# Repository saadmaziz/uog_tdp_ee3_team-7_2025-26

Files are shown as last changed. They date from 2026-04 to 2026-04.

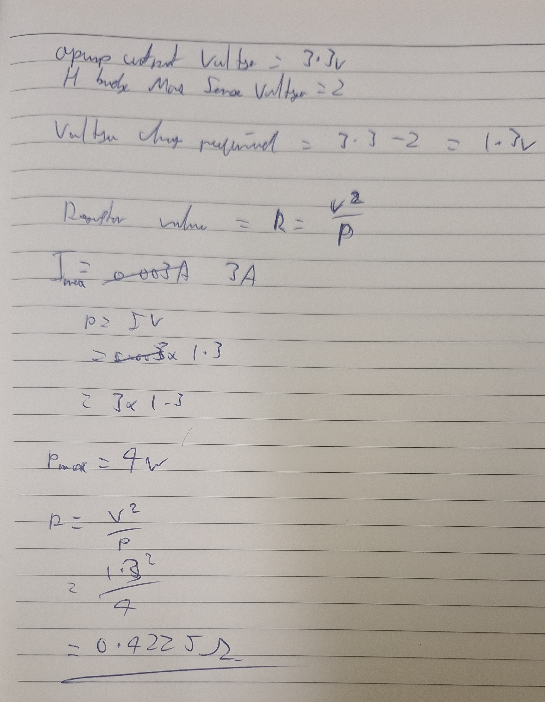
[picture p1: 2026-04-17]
5 - Research, Datasheets, and Manuals/5-1 - Research/calculations/H-bridge resistor calculation.jpg

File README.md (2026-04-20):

# UoG_TDP-EE3_Team_7
Design Files for the 3rd year EEE team design project at the University of Glasgow. Line following rover, with obstacle avoidance, traffic lights detection, remote control using an ESP-32 connected to a laptop and a Logitech 3D Pro Joystick.
The  Centeral processor is a Freescale NXP Frdm KL25Z.

1 - Team Organisation and 6 - General Documents are not uploaded as they may contain non-relavant information that should not be made public

The team consisted of 5 members.

My personal contributions spanned all of the software, all of the mechanical design, a substantial part of the electronic hardware design, and most of the integration.

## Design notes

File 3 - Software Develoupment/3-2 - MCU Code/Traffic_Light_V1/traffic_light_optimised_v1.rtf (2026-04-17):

#include "mbed.h"

#include <algorithm> // std::max

#include <cmath> // roundf

// 7-bit I2C address is 0x10; mbed I2C wants 8-bit address (shifted left)
#define VEML3328_ADDR (0x10 << 1) // 0x20

#define REG_CONFIG 0x00

#define REG_R_DATA 0x05

#define REG_G_DATA 0x06

#define REG_B_DATA 0x07

I2C i2c(PTC2, PTC1);

PwmOut led_R(LED_RED);
PwmOut led_G(LED_GREEN);
PwmOut led_B(LED_BLUE);

// Tuning knobs
static const float PWM_PERIOD_S = 0.001f; // 1 kHz PWM
static const float EMA_ALPHA = 0.25f; // 0..1 (higher = more responsive, lower = smoother)
static const float MIN_SCALE = 50.0f; // prevents divide-by-zero
static const int ROUND_STEPS = 30; // your roundingfactor

static inline float clamp01(float x) {
if (x < 0.0f) return 0.0f;
if (x > 1.0f) return 1.0f;
return x;
}

uint16_t read_reg(uint8_t reg) {
char cmd[1] = { (char)reg };
char data[2] = { 0, 0 };

int w = i2c.write(VEML3328_ADDR, cmd, 1, true);
int r = i2c.read(VEML3328_ADDR, data, 2, false);

if (w != 0 || r != 0) {
return 0; // basic fail-safe
}

return (uint16_t)((uint8_t)data[1] << 8) | (uint8_t)data[0];
}

int main() {
// I2C speed
i2c.frequency(400000); // 400 kHz

// Sensor config: 0x0000 (powers on, default gain/IT per datasheet defaults)
char config_cmd[3] = { REG_CONFIG, 0x00, 0x00 };
i2c.write(VEML3328_ADDR, config_cmd, 3, false);

// PWM setup (ALL channels)
led_R.period(PWM_PERIOD_S);
led_G.period(PWM_PERIOD_S);
led_B.period(PWM_PERIOD_S);

// EMA filtered values
float r_f = 0.0f, g_f = 0.0f, b_f = 0.0f;

while (true) {
uint16_t r_raw = read_reg(REG_R_DATA);
uint16_t g_raw = read_reg(REG_G_DATA);
uint16_t b_raw = read_reg(REG_B_DATA);

// Smooth raw readings
r_f = (1.0f - EMA_ALPHA) * r_f + EMA_ALPHA * (float)r_raw;
g_f = (1.0f - EMA_ALPHA) * g_f + EMA_ALPHA * (float)g_raw;
b_f = (1.0f - EMA_ALPHA) * b_f + EMA_ALPHA * (float)b_raw;

// Auto-scale
float max_rgb = std::max({r_f, g_f, b_f});
if (max_rgb < MIN_SCALE) max_rgb = MIN_SCALE;

float r_norm = r_f / max_rgb;
float g_norm = g_f / max_rgb;
float b_norm = b_f / max_rgb;

// Rounding
r_norm = roundf(r_norm * ROUND_STEPS) / ROUND_STEPS;
g_norm = roundf(g_norm * ROUND_STEPS) / ROUND_STEPS;
b_norm = roundf(b_norm * ROUND_STEPS) / ROUND_STEPS;

r_norm = clamp01(r_norm);
g_norm = clamp01(g_norm);
b_norm = clamp01(b_norm);

// KL25Z LEDs are active low
led_R = 1.0f - r_norm;
led_G = 1.0f - g_norm;
led_B = 1.0f - b_norm;

ThisThread::sleep_for(50ms); // quicker refresh
}
}

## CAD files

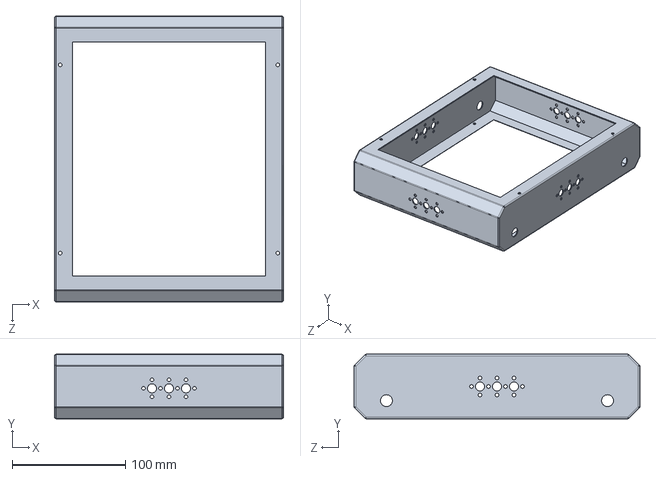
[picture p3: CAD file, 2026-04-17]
4 - Mechanical CAD/Chassis/Main Chassis.SLDPRT
202.0 x 57.0 x 252.0 mm

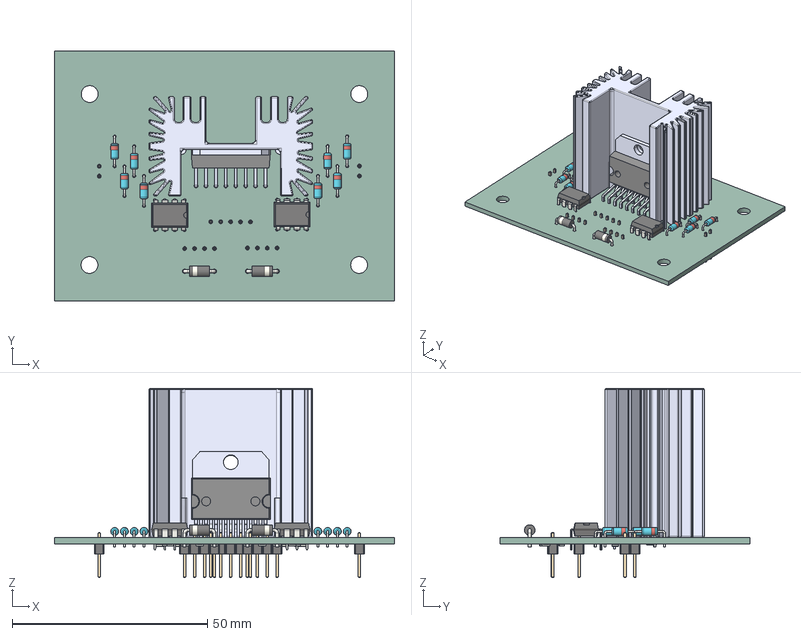
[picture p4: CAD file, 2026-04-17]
2 - PCB Files/2-1 - Distribution Board/Distribution Board V2/$tempfile$.step
87.0 x 64.0 x 48.4 mm
D_DO-35_SOD27_P7.62mm_Horizontal x 8
D_DO-41_SOD81_P7.62mm_Horizontal x 2
DIP-8_W7.62mm x 2
L298N
36-0275_Heatsink
PinHeader_1x04_P2.54mm_Vertical x 2
PinHeader_1x02_P2.54mm_Vertical x 2
R_0805_2012Metric x 10
PinHeader_1x05_P2.54mm_Vertical
C_0805_2012Metric x 2
R_1206_3216Metric x 4
TDP3_T7_H-Bridge_V-3_PCB

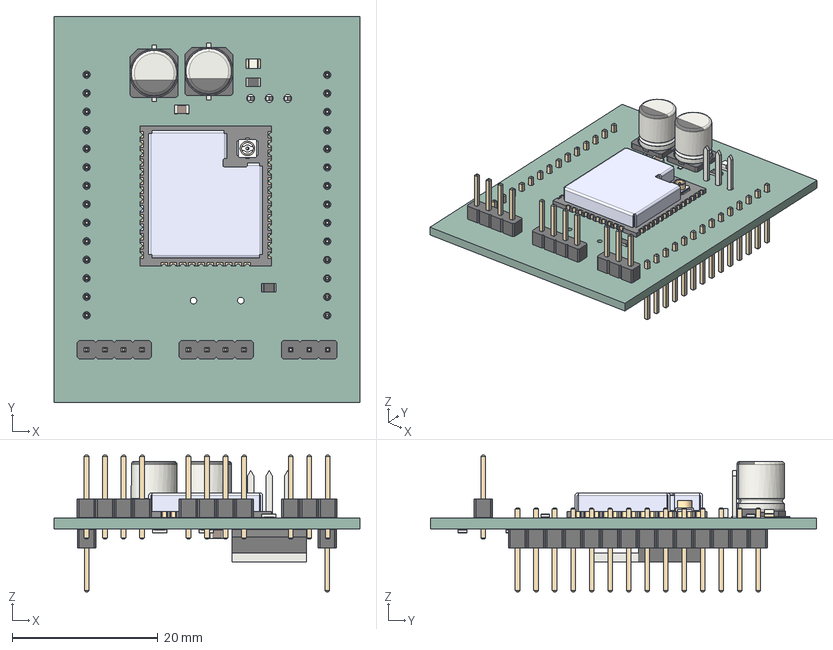
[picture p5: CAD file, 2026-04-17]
2 - PCB Files/2-1 - Distribution Board/Distribution Board V2/PCBs/ESP32-Breakout V1.step
42.0 x 53.0 x 18.8 mm
LED_0805_2012Metric
CP_Elec_6.3x7.7 x 2
PinHeader_1x04_P2.54mm_Vertical x 2
R_0805_2012Metric x 4
ESP32-WROOM-32UE-N4
C_0805_2012Metric x 3
PinHeader_1x03_P2.54mm_Vertical
PinHeader_1x14_P2.54mm_Vertical x 2
TO-220-3_Horizontal_TabUp
ESP32_Breakout V1_PCB

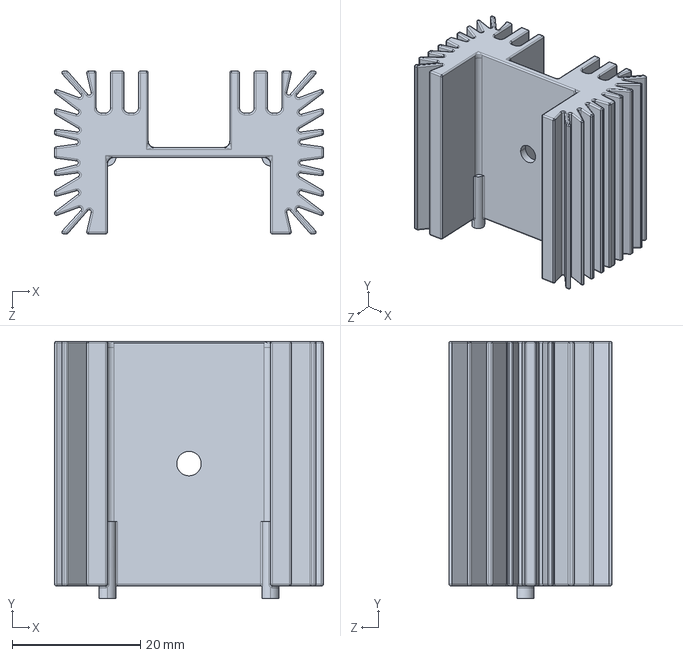
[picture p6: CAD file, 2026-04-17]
2 - PCB Files/2-2 - Motor Driver/heatsink.STEP
41.9 x 40.1 x 25.4 mm

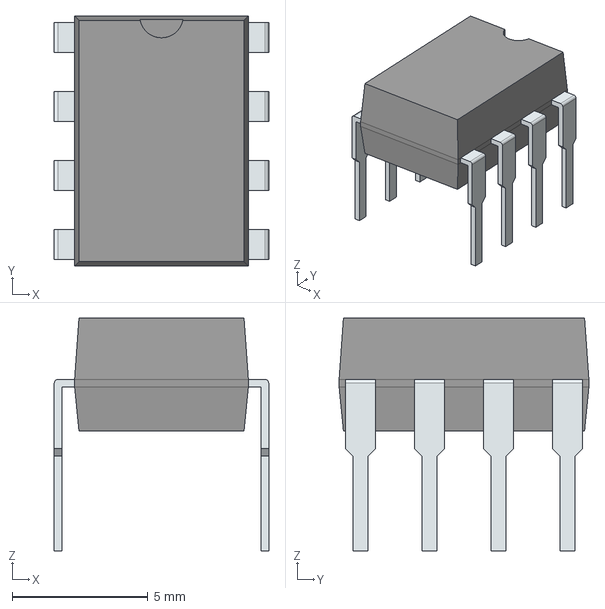
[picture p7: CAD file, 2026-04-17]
2 - PCB Files/2-2 - Motor Driver/TDP3_T7_H-Bridge_V-3/TDP3_T7_H-Bridge_V-3/LF353N.stp
7.90 x 9.20 x 8.58 mm
PinsArrayLR

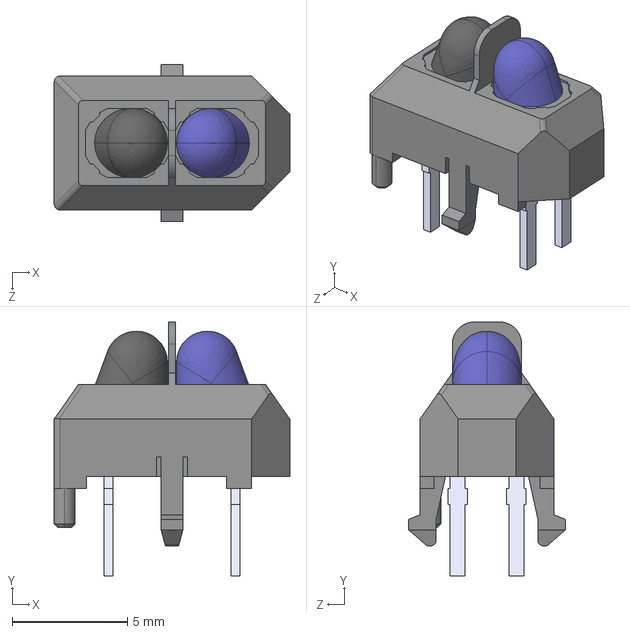
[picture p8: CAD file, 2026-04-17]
2 - PCB Files/2-3 - Line Following/Line following V3/TCRT5000.stp
10.2 x 11.0 x 6.80 mm

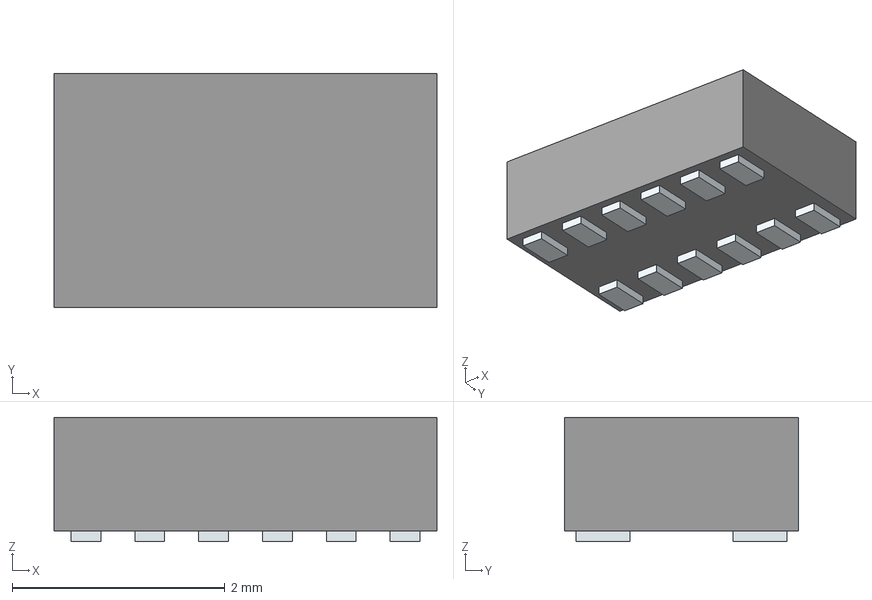
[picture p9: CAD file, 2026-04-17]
2 - PCB Files/2-5 - Obstacle Avoidance/Breakout OSRAM_TMF8806-1AM V1/TMF8806/TMF8806-1AM_OLGA12_LF_T&RDP.stp
3.60 x 2.20 x 1.17 mm
Pins

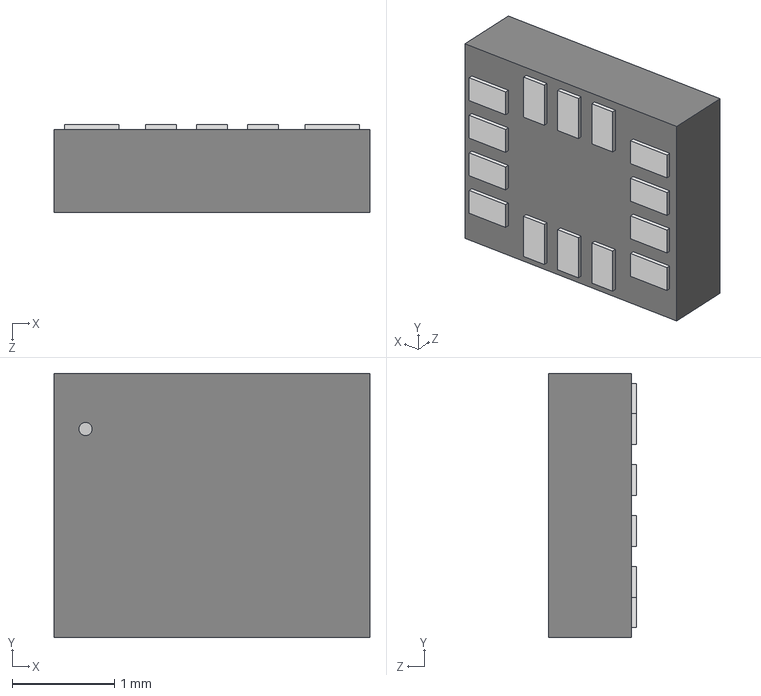
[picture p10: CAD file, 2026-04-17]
2 - PCB Files/2-5 - Obstacle Avoidance/Breakout STM-LSM6DSOQTR V1/LSM6DSO.stp
3.10 x 2.59 x 0.866 mm

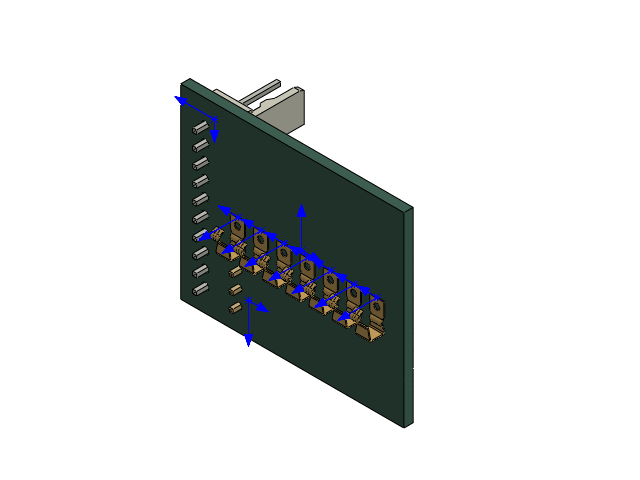
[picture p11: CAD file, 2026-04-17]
4 - Mechanical CAD/PCBs/LiDAR/Slip Ring Static Contacts PCB V2 SLD1.SLDASM
S7171-45R.step x 7
Molex_KK-254_AE-6410-10A_1x10_P2.54mm_Vertical.step
PinHeader_1x03_P2.54mm_Vertical.step
Slip Ring Stactic Contacts V2_PCB.step

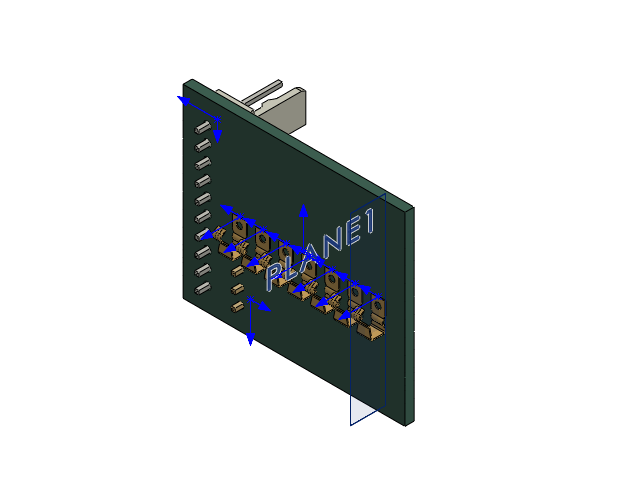
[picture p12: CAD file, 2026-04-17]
4 - Mechanical CAD/LiDAR(Sonar)/V2/PCBs/Slip Ring Static Contacts PCB V2 SLD1/Slip Ring Static Contacts PCB V2 SLD1.SLDASM
S7171-45R.step x 7
Molex_KK-254_AE-6410-10A_1x10_P2.54mm_Vertical.step
PinHeader_1x03_P2.54mm_Vertical.step
Slip Ring Stactic Contacts V2_PCB.step

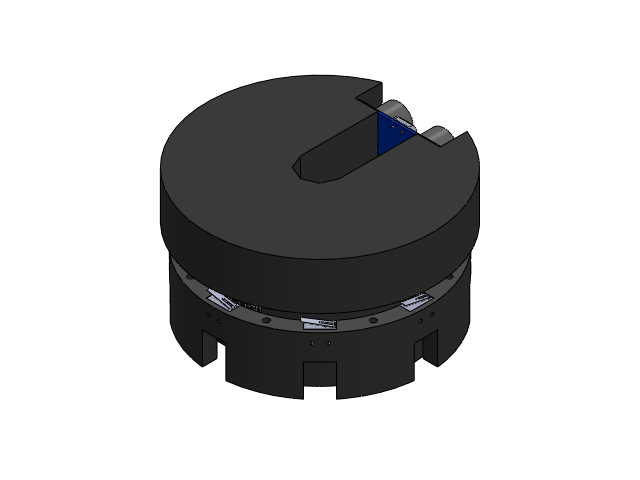
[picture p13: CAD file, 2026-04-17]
4 - Mechanical CAD/LiDAR(Sonar)/V2/Sonar Assembly.SLDASM
Base
FS09R_Servo_Motor
AC6000Z-ISB_Bearing
S7171-45R.step x 7
Molex_KK-254_AE-6410-10A_1x10_P2.54mm_Vertical.step
PinHeader_1x03_P2.54mm_Vertical.step
Slip Ring Stactic Contacts V2_PCB.step
Slip Ring Rotating Contacts V2_PCB.step
Center
Spinny_Top
Switch holder
Encoding Switch x 8
Switch Peg
Ultrasonic sensor

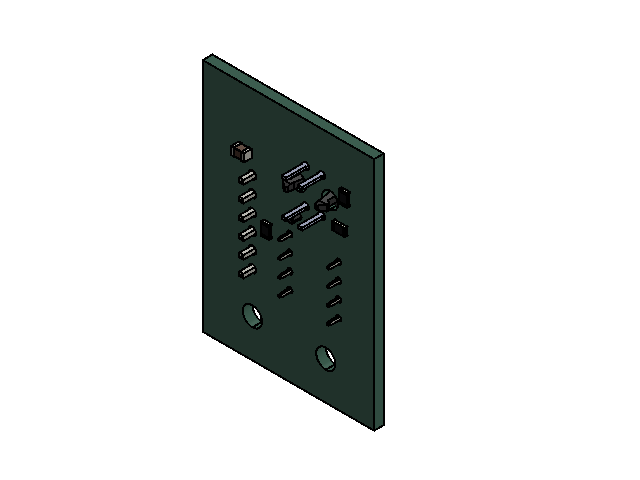
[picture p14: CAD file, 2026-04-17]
4 - Mechanical CAD/Line Sensors/Line Following Side.SLDASM
C_0805_2012Metric_1.step
R_0805_2012Metric_1.step x 3
Molex_KK-254_AE-6410-06A_1x06_P2.54mm_Vertical.step
TCRT5000_1.step
DIP-8_W7.62mm_1.step
Line following V3_PCB.step

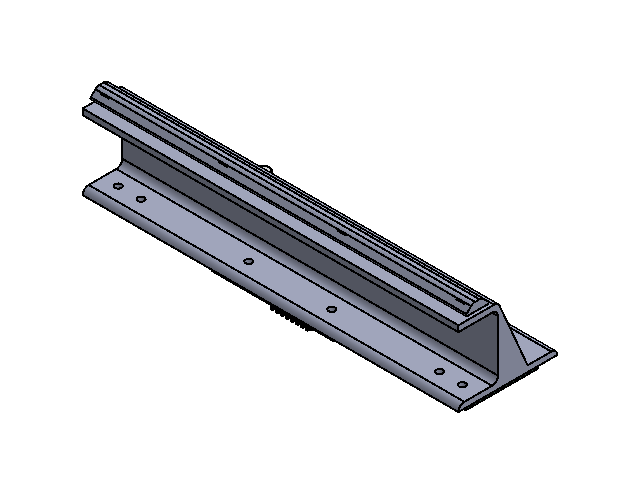
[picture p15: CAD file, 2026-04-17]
4 - Mechanical CAD/Line Sensors/Line Following Assem.SLDASM
Mount
R_0805_2012Metric.step x 12
C_0805_2012Metric.step x 2
TCRT5000.step x 3
DIP-8_W7.62mm.step x 3
Molex_KK-254_AE-6410-08A_1x08_P2.54mm_Vertical.step
Line following V2_PCB.step
Molex_KK-254_AE-6410-06A_1x06_P2.54mm_Vertical_1.step
TCRT5000_2.step
DIP-8_W7.62mm_2.step
C_0805_2012Metric_2.step
R_0805_2012Metric_2.step x 3
Line following V3_PCB_1.step
Pot
C_0805_2012Metric_1.step
R_0805_2012Metric_1.step x 3
Molex_KK-254_AE-6410-06A_1x06_P2.54mm_Vertical.step
TCRT5000_1.step
DIP-8_W7.62mm_1.step
Line following V3_PCB.step
Nut_Holder

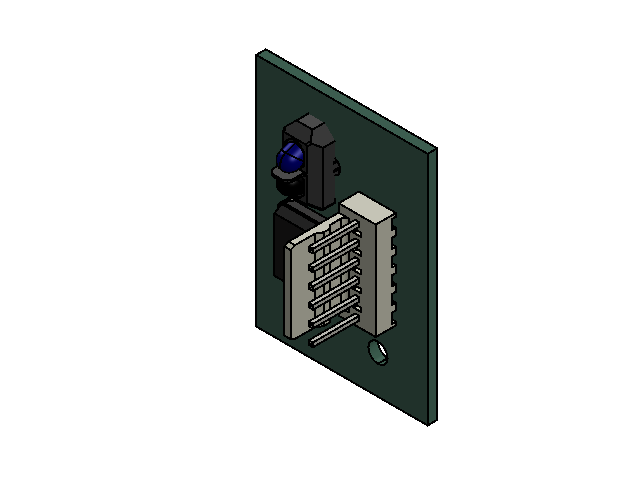
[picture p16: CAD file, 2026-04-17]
4 - Mechanical CAD/Line Sensors/Line Following Side mirrored.SLDASM
Molex_KK-254_AE-6410-06A_1x06_P2.54mm_Vertical_1.step
TCRT5000_2.step
DIP-8_W7.62mm_2.step
C_0805_2012Metric_2.step
R_0805_2012Metric_2.step x 3
Line following V3_PCB_1.step

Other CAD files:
4 - Mechanical CAD/LiDAR(Sonar)/V2/PCBs/Slip Ring Rotating Contacts PCB V2 SLD/Slip Ring Rotating Contacts PCB V2 SLD.SLDASM
4 - Mechanical CAD/Scissor Jack/Assem.SLDASM
4 - Mechanical CAD/PCBs/LiDAR/Slip Ring Rotating Contacts PCB V2 SLD.SLDASM
4 - Mechanical CAD/Line Sensors/Line Following Center.SLDASM
2 - PCB Files/2-1 - Distribution Board/Distribution Board V2/PCBs/Motor-Controller.step
2 - PCB Files/2-1 - Distribution Board/Distribution Board V2/PCBs/Power-Supply.step
2 - PCB Files/2-2 - Motor Driver/36-0275_Heatsink.STEP
2 - PCB Files/2-2 - Motor Driver/L298N.stp
2 - PCB Files/2-5 - Obstacle Avoidance/LiDAR Distance Measurement V1/TMF8806/Breakout OSRAM_TMF8806-1AM V1.step
2 - PCB Files/2-5 - Obstacle Avoidance/LiDar Baseboard (Angle Measurement) V1/Breakout STM-LSM6DSOQTR V1.step
2 - PCB Files/2-5 - Obstacle Avoidance/LiDar Baseboard (Angle Measurement) V1/LSM6DSOTR.stp
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

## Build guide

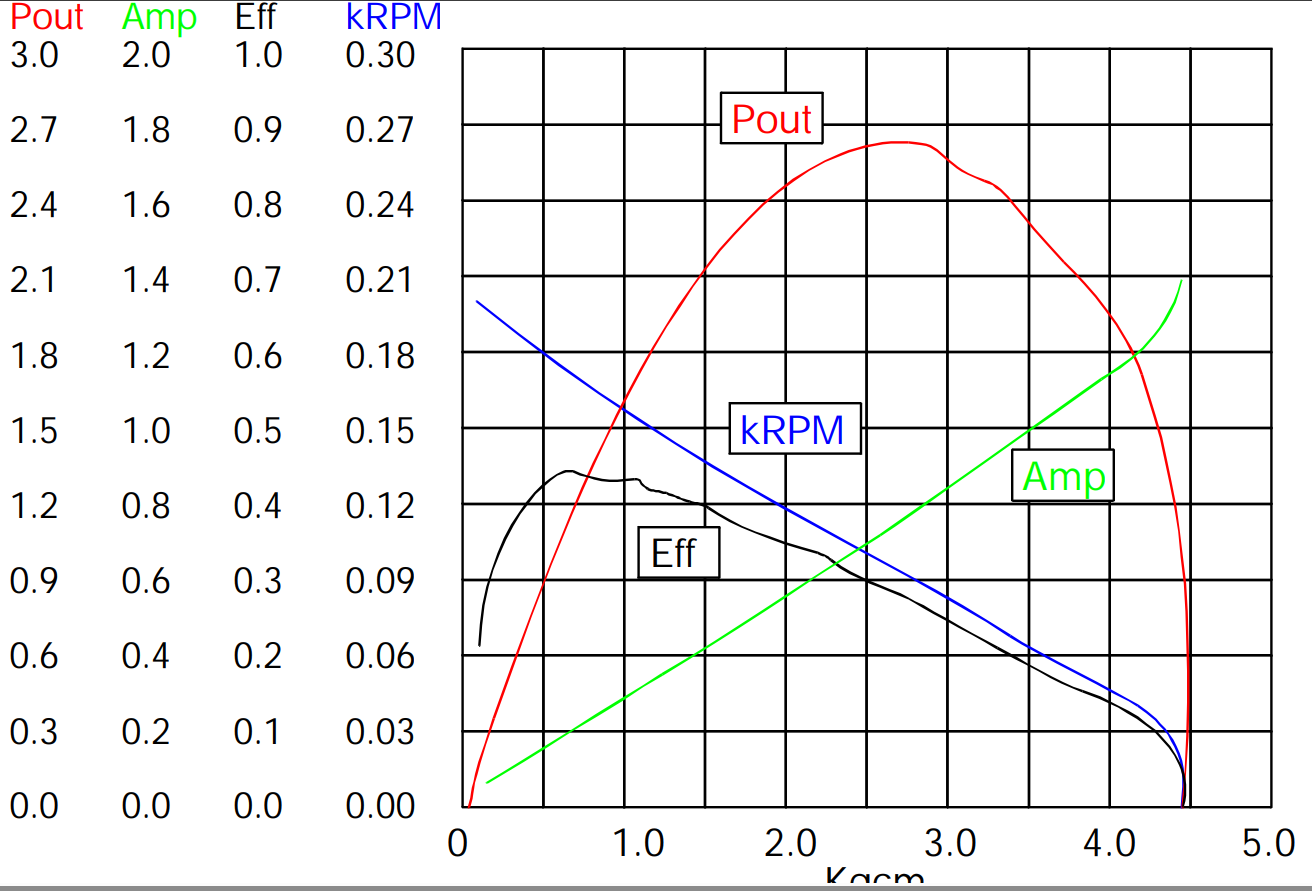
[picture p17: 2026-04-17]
5 - Research, Datasheets, and Manuals/5-1 - Research/Motor Curves/Motor Plot.PNG

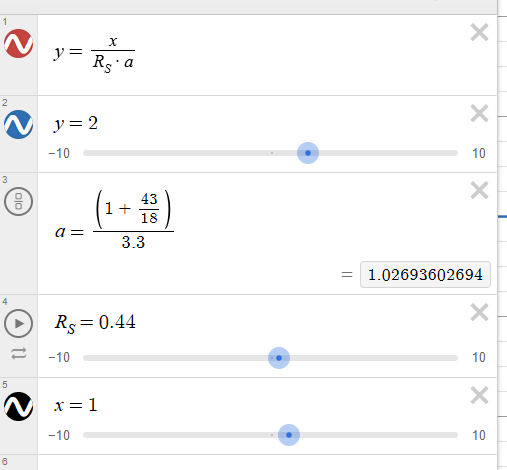
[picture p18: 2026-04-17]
5 - Research, Datasheets, and Manuals/5-1 - Research/Motor Curves/I-RPM transfrer.PNG

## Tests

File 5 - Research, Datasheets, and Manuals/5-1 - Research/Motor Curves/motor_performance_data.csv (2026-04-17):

Torque (Kgcm) | Pout (Output Power) | Amp (Current) | Eff (Efficiency) | kRPM (Speed)
0 | 0 | 0 | 0 | 200
0.5 | 0.85 | 0.32 | 0.44 | 178
1 | 1.55 | 0.53 | 0.42 | 155
1.5 | 2.1 | 0.74 | 0.38 | 133
2 | 2.45 | 0.95 | 0.34 | 111
2.5 | 2.65 | 1.16 | 0.3 | 89
3 | 2.55 | 1.37 | 0.24 | 67
3.5 | 2.2 | 1.58 | 0.18 | 44
4 | 1.6 | 1.79 | 0.12 | 22
4.5 | 0 | 2 | 0 | 0
 | 2.65
 | y = -97.659x + 200

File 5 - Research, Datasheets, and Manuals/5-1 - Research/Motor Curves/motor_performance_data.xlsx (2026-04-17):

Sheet: motor_performance_data
Torque (Kgcm) | Pout (Output Power) | Amp (Current) | Eff (Efficiency) | RPM (Speed)
0 | 0 | 0 | 0 | 200
0.5 | 0.85 | 0.32 | 0.44 | 178
1 | 1.55 | 0.53 | 0.42 | 155
1.5 | 2.1 | 0.74 | 0.38 | 133
2 | 2.45 | 0.95 | 0.34 | 111
2.5 | 2.65 | 1.16 | 0.3 | 89
3 | 2.55 | 1.37 | 0.24 | 67
3.5 | 2.2 | 1.58 | 0.18 | 44
4 | 1.6 | 1.79 | 0.12 | 22
4.5 | 0 | 2 | 0 | 0
 | 2.65
 | I to RPM | RPM to M/S
 | y = -97.659x + 200 | M/s = RPM* 0.012566
 | 1.9
 | 14.4479

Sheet: Sheet1
Amp (Current) | Torque (Kgcm)
0 | 0
0.32 | 0.5
0.53 | 1
0.74 | 1.5
0.95 | 2
1.16 | 2.5
1.37 | 3
1.58 | 3.5
1.79 | 4
2 | 4.5

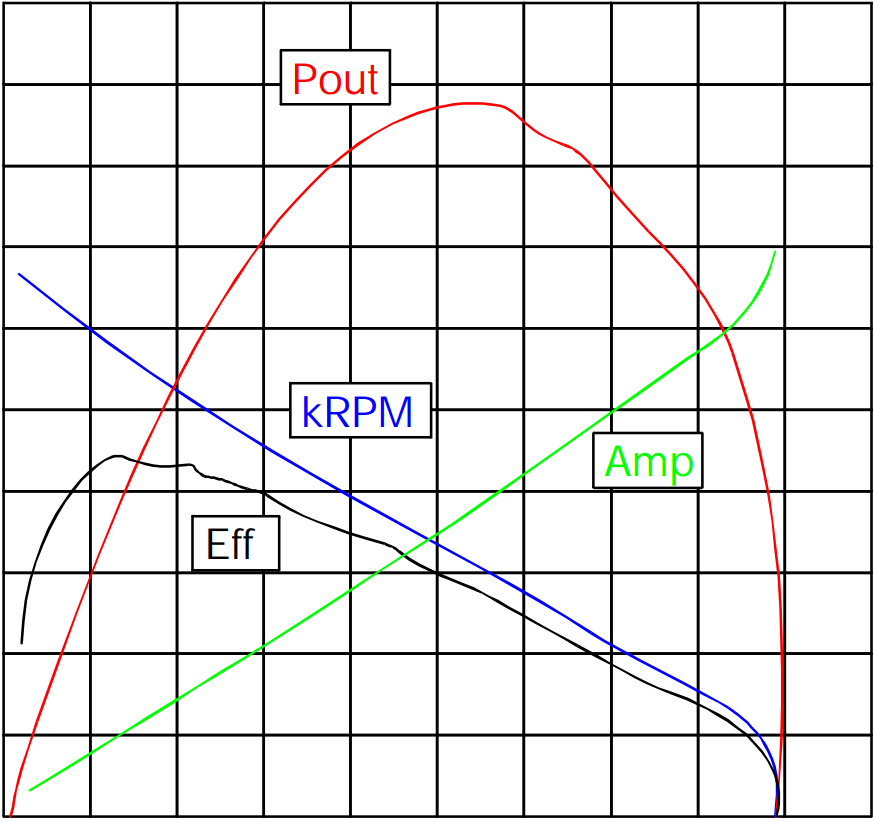
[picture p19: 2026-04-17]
5 - Research, Datasheets, and Manuals/5-1 - Research/Position measurement/Motor Plot.PNG

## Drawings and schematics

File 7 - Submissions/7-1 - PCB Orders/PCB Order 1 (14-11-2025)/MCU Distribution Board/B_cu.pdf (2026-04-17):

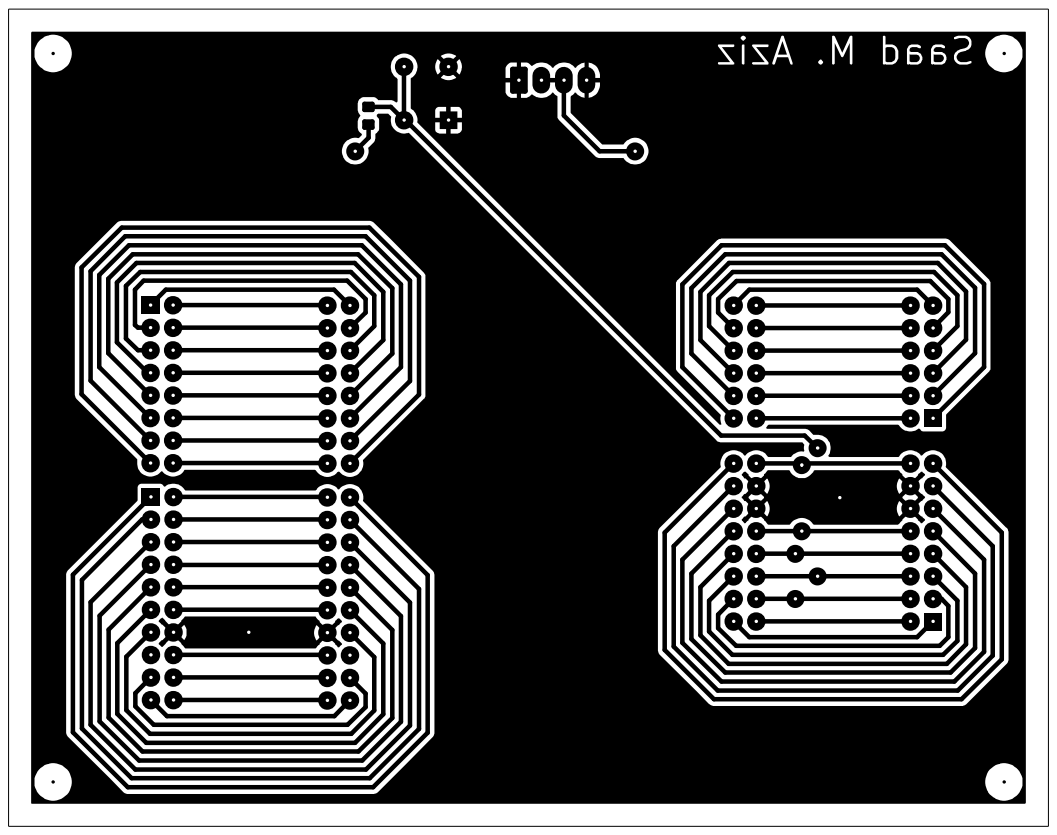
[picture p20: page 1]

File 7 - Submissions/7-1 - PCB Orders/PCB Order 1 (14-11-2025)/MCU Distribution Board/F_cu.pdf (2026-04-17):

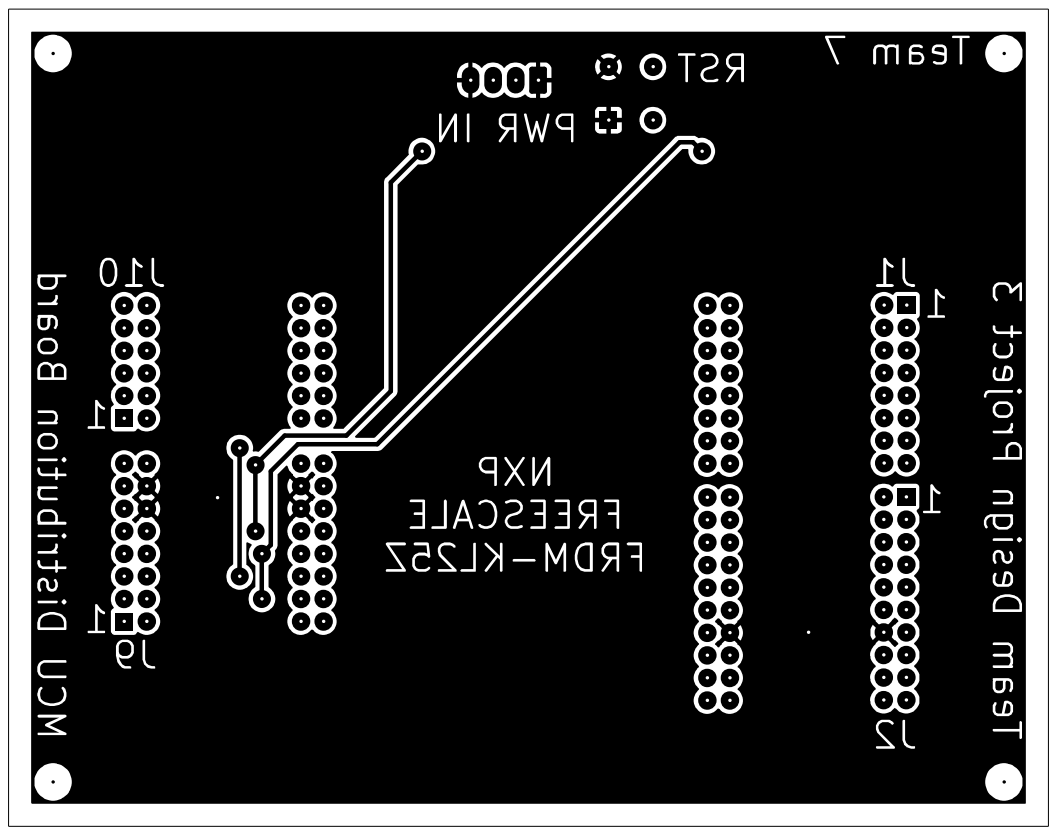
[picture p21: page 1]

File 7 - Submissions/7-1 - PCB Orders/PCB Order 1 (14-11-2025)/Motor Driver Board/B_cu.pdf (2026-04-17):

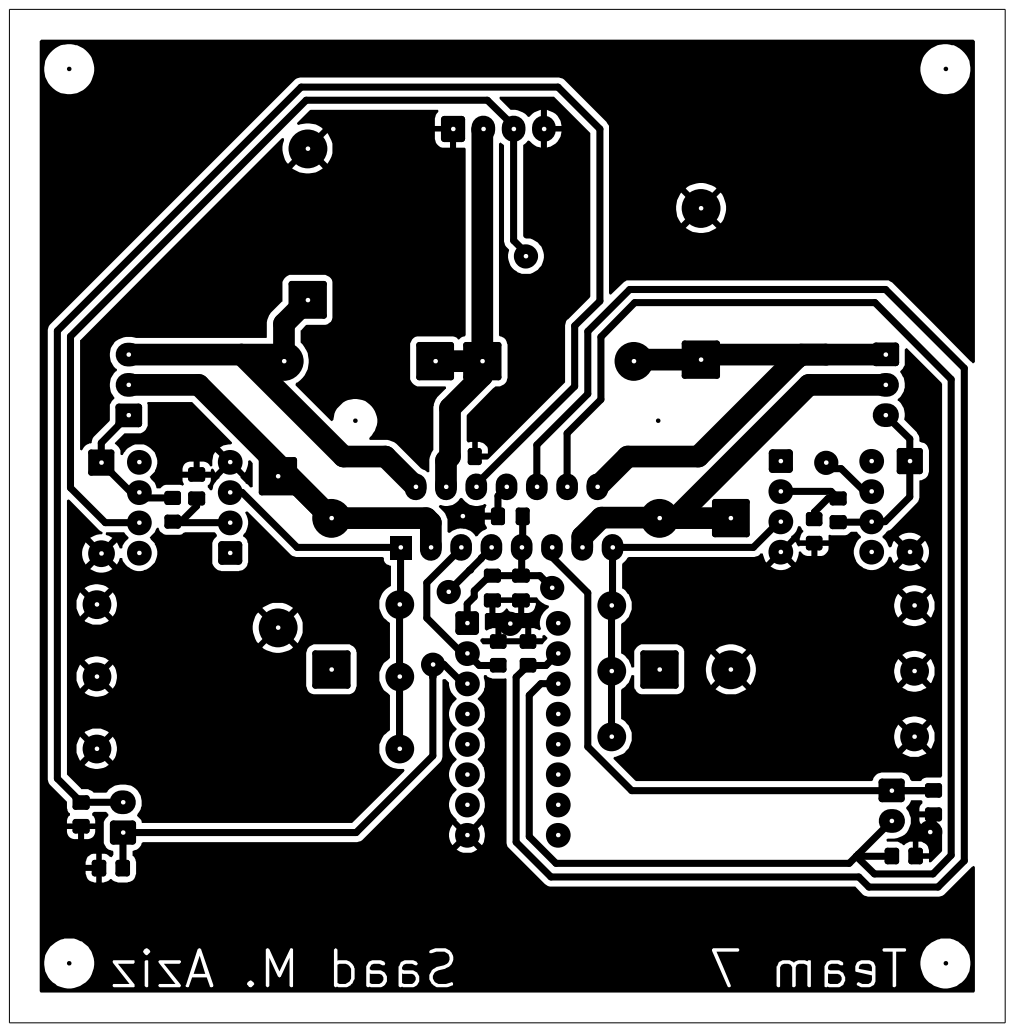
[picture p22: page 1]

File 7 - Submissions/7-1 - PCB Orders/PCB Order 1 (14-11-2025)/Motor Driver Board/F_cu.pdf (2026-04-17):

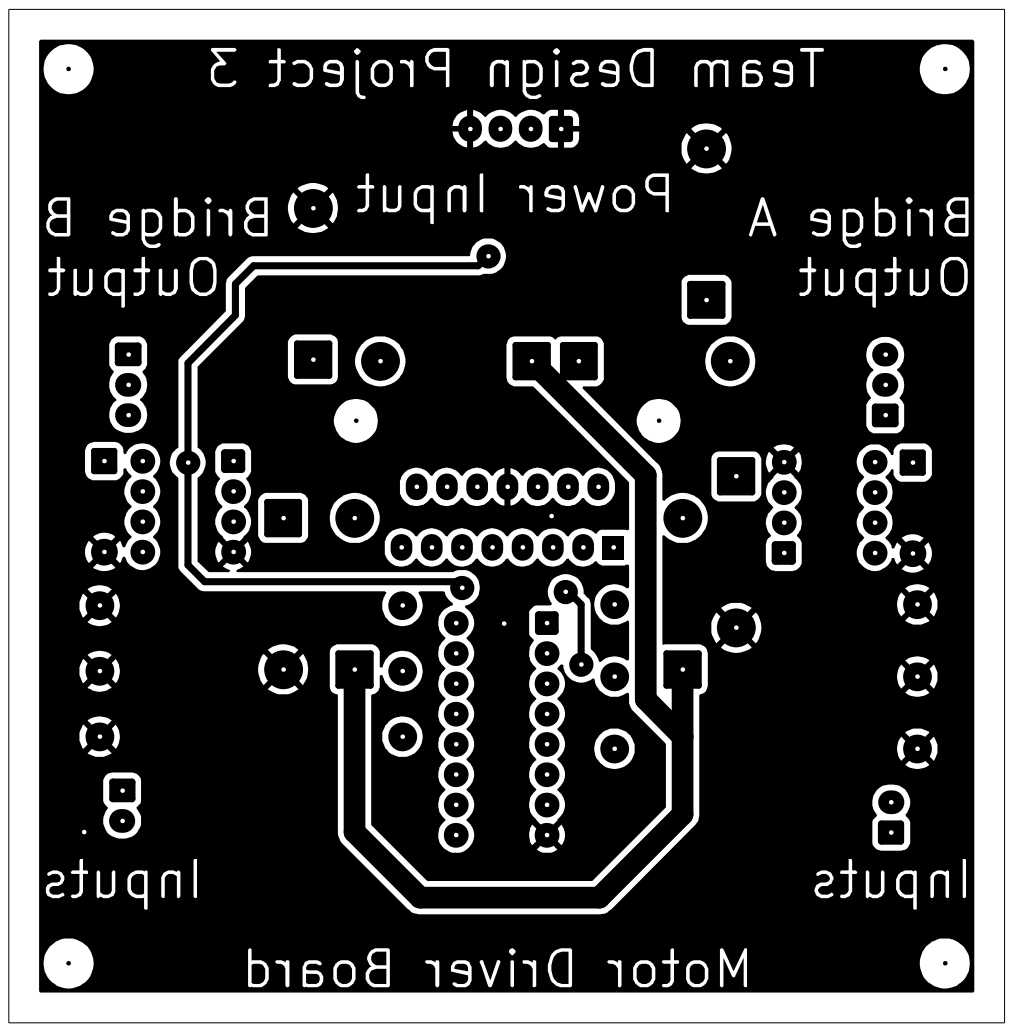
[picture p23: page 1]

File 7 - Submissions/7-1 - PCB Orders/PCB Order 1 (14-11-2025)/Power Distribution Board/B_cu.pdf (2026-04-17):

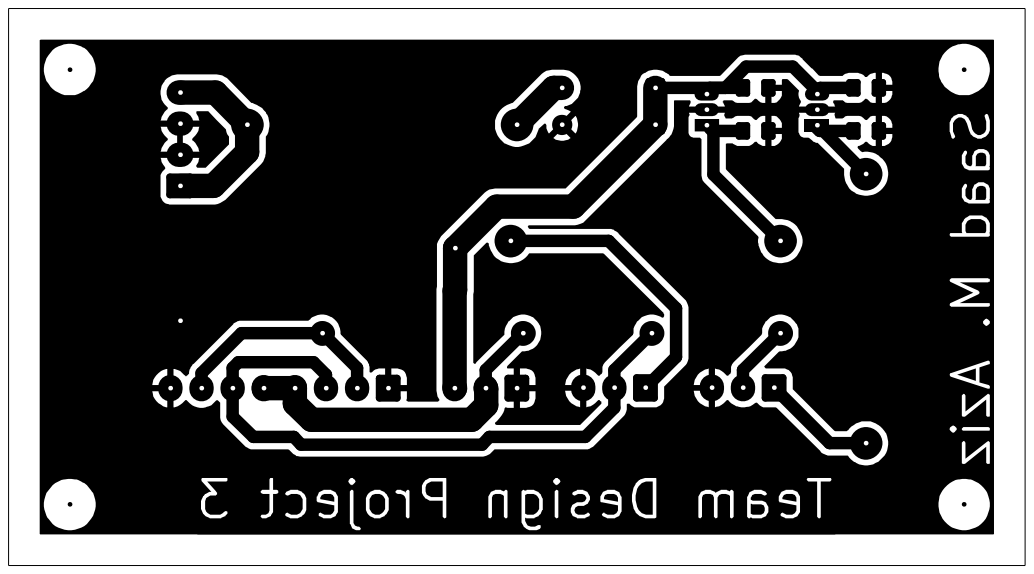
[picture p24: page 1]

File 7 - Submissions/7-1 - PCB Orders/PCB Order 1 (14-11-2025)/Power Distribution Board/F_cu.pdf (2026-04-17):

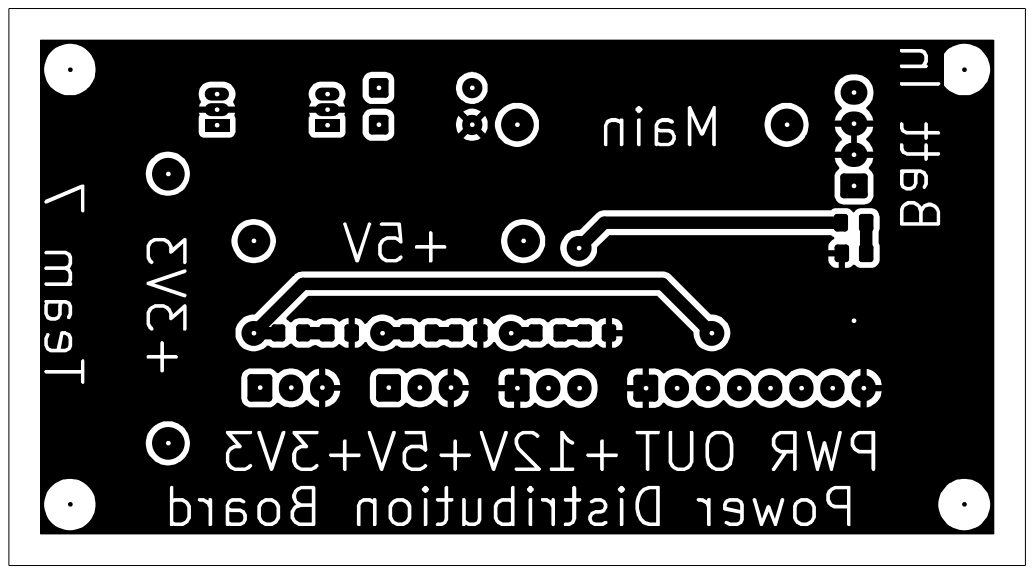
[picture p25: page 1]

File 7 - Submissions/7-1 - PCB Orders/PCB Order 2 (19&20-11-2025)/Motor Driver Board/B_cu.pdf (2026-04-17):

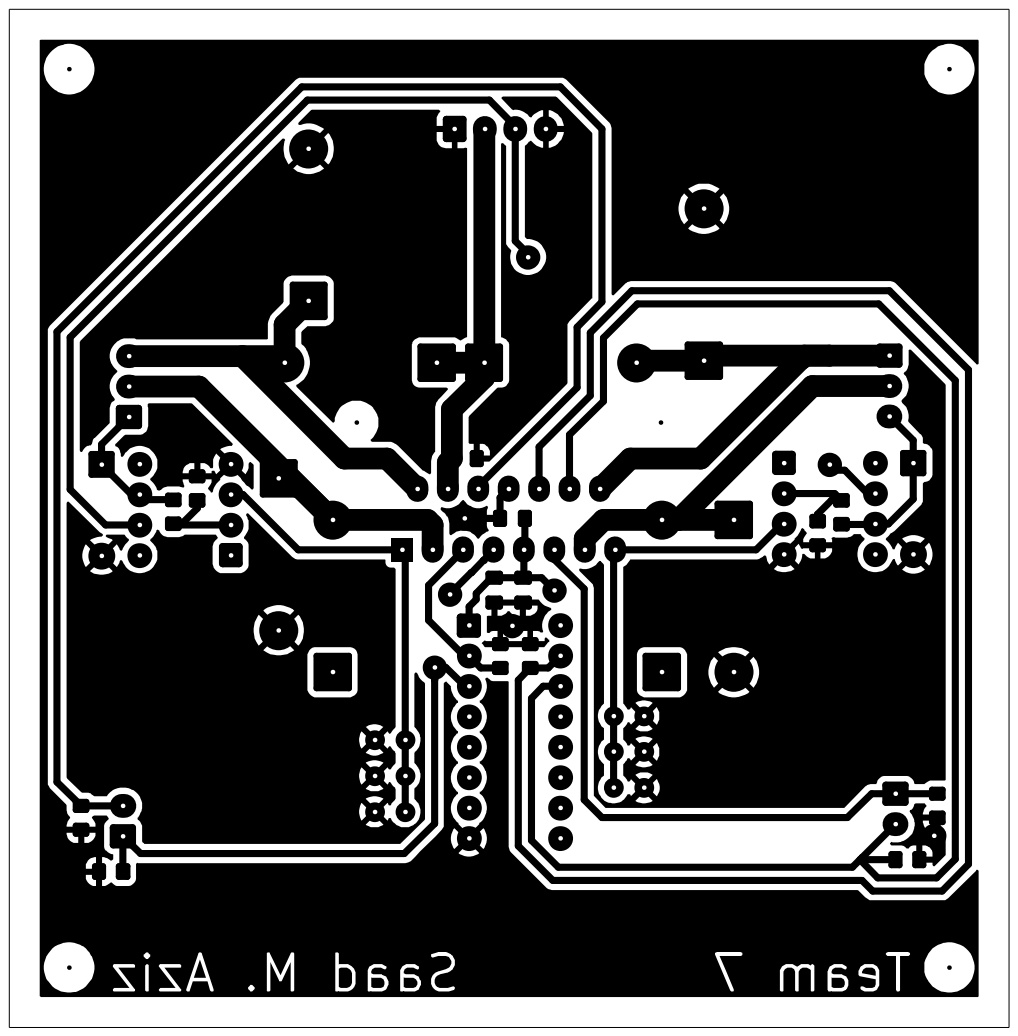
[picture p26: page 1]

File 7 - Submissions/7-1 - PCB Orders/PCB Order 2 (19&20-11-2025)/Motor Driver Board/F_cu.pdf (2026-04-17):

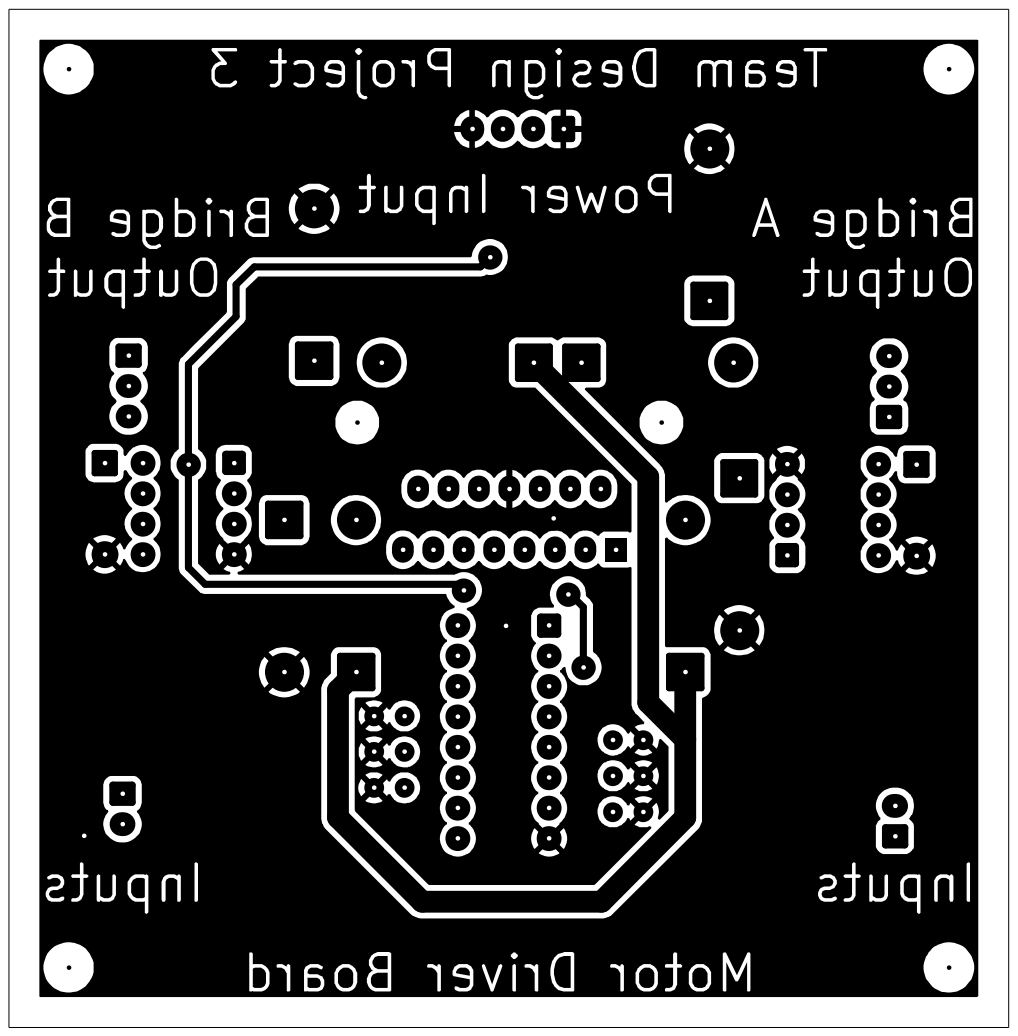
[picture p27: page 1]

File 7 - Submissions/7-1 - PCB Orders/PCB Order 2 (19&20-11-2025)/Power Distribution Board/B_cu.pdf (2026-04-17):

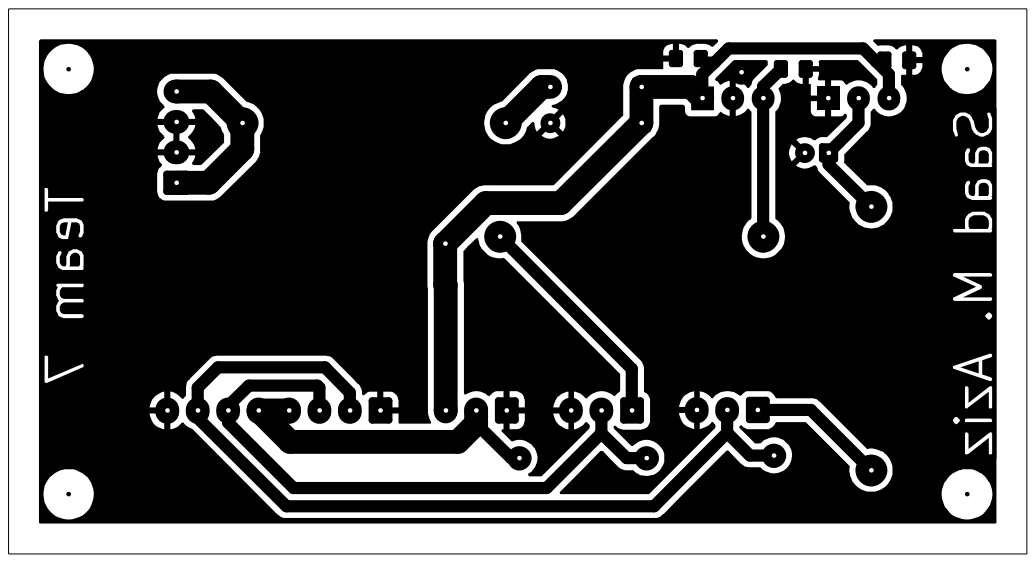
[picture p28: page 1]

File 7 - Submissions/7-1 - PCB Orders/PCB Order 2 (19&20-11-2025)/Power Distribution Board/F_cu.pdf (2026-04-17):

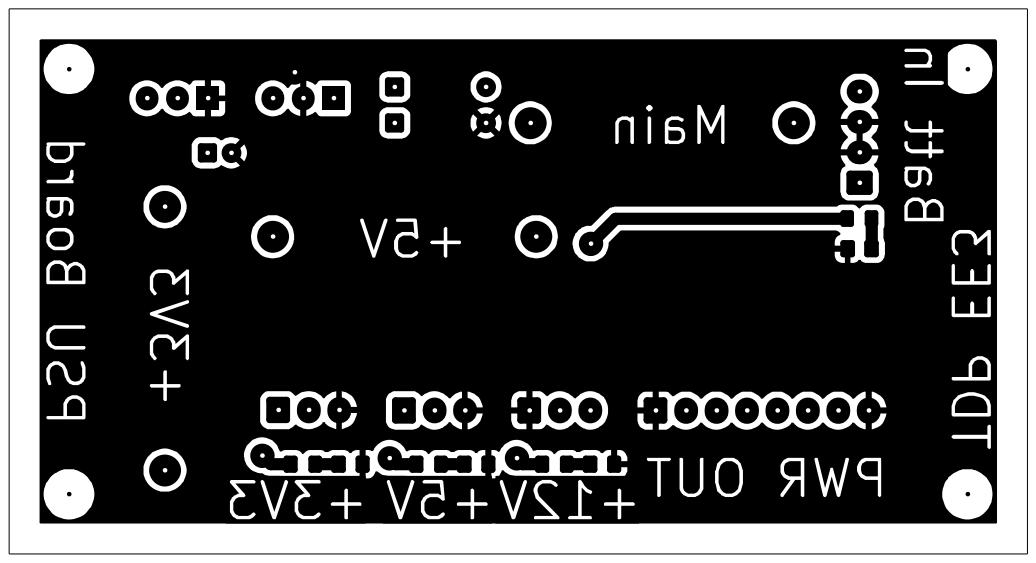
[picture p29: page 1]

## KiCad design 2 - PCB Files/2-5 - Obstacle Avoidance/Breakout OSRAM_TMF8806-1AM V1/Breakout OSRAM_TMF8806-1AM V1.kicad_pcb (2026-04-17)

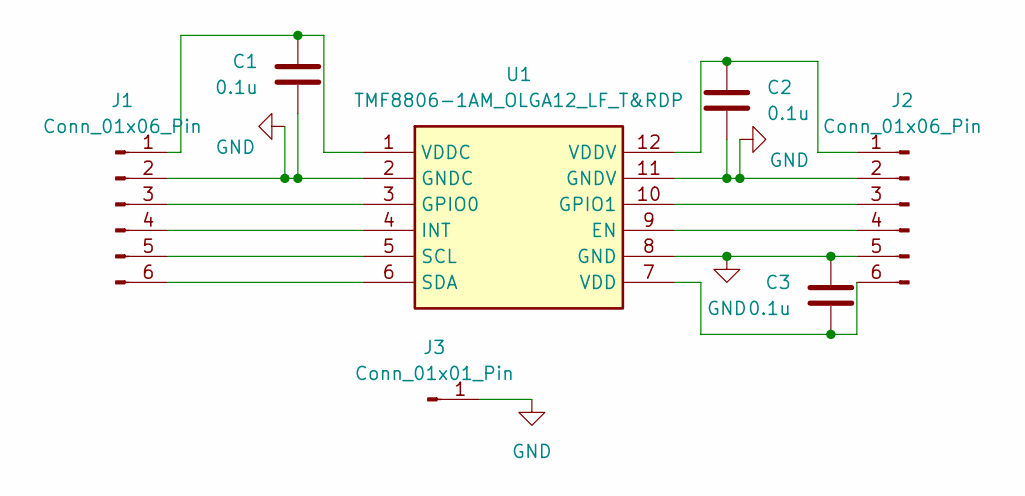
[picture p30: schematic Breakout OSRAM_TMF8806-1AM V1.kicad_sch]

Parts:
C1, C2, C3: 0.1u; C_0603_1608Metric
J1, J2: Conn_01x06_Pin; PinHeader_1x06_P2.54mm_Vertical
J3: Conn_01x01_Pin; PinHeader_1x01_P2.54mm_Vertical
U1: TMF8806-1AM_OLGA12_LF_T&RDP; TMF88061AMOLGA12LFTRDP; Manufacturer_Part_Number TMF8806-1AM OLGA12 LF T&RDP

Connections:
GND: C1.2, C2.2, C3.1, J1.2, J2.2, J2.5, J3.1, U1.2 (GNDC), U1.8 (GND), U1.11 (GNDV)
unnamed: C1.1, J1.1, U1.1 (VDDC)
unnamed: J1.3, U1.3 (GPIO0)
unnamed: J1.4, U1.4 (INT)
unnamed: J1.5, U1.5 (SCL)
unnamed: J1.6, U1.6 (SDA)
unnamed: C2.1, J2.1, U1.12 (VDDV)
unnamed: J2.3, U1.10 (GPIO1)
unnamed: J2.4, U1.9 (EN)
unnamed: C3.2, J2.6, U1.7 (VDD)

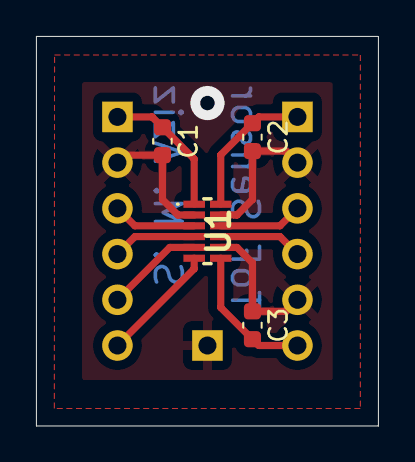
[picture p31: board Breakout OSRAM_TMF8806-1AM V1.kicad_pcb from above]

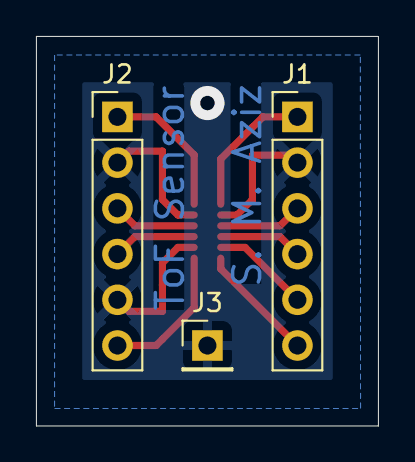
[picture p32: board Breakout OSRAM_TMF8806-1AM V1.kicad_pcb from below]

Board: 2 copper layers, 19.0 x 21.6 mm, 7 parts (3 on the bottom side), 10 nets.

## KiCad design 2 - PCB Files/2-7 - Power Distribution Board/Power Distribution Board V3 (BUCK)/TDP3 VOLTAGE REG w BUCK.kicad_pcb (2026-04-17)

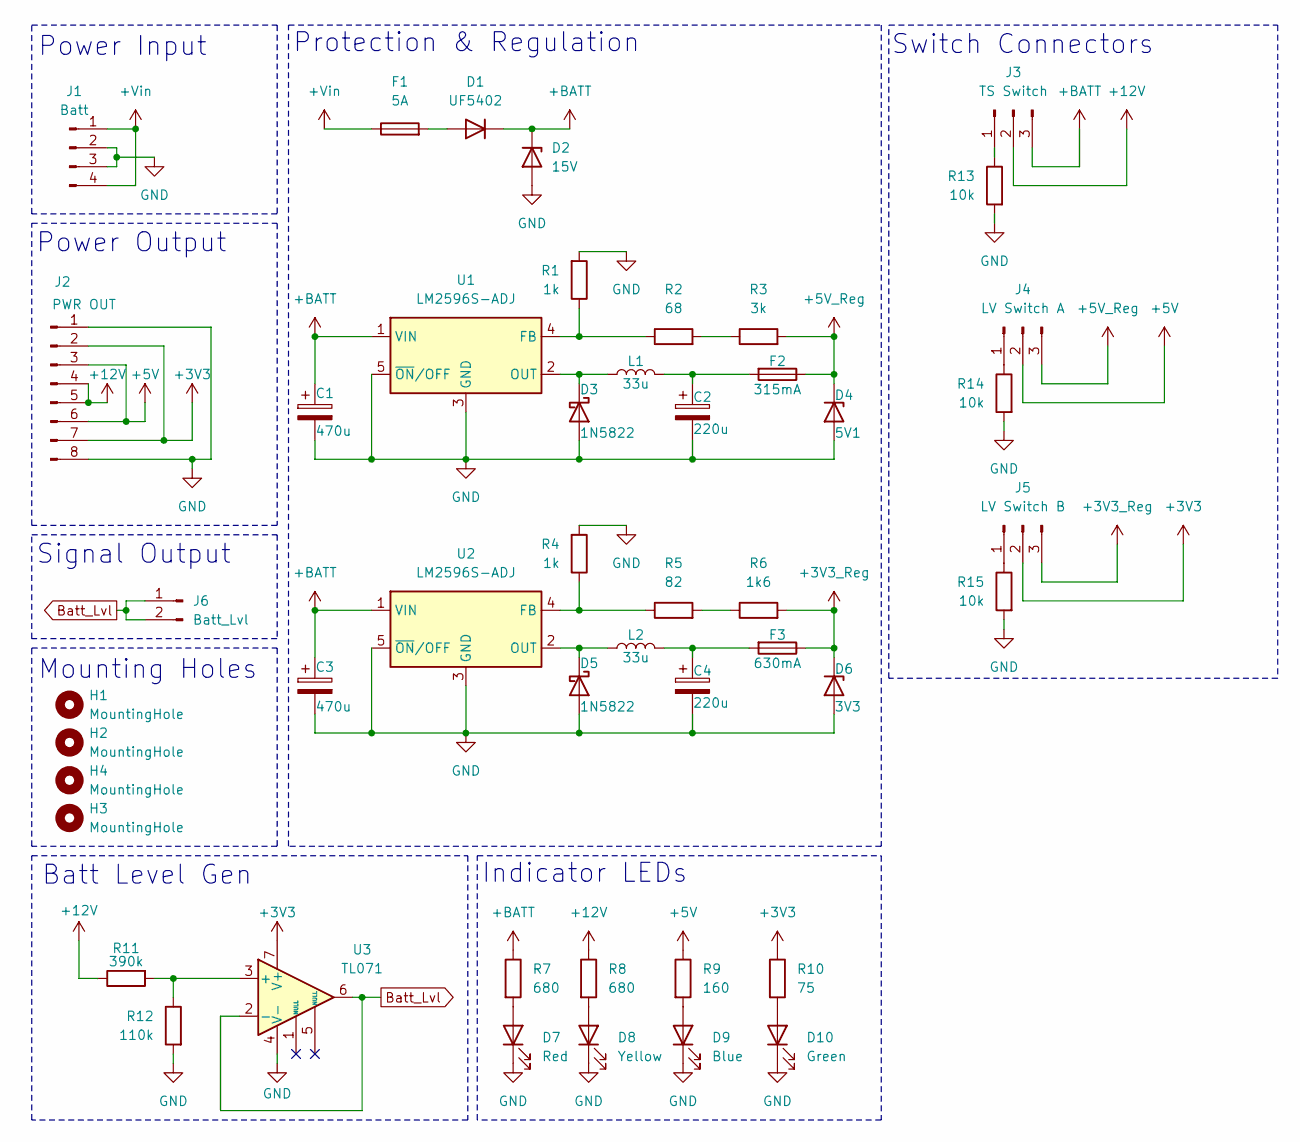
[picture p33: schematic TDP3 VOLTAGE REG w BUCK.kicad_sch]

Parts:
C1, C3: 470u; CP_Radial_D13.0mm_P5.00mm
C2, C4: 220u; CP_Radial_D10.0mm_P5.00mm
D1: UF5402; D_DO-201AD_P15.24mm_Horizontal
D2: 15V; D_DO-35_SOD27_P7.62mm_Horizontal
D3, D5: 1N5822; D_DO-201AD_P15.24mm_Horizontal
D4: 5V1; D_DO-35_SOD27_P7.62mm_Horizontal
D6: 3V3; D_DO-35_SOD27_P7.62mm_Horizontal
D7: Red; LED_0805_2012Metric_Pad1.15x1.40mm_HandSolder
D8: Yellow; LED_0805_2012Metric_Pad1.15x1.40mm_HandSolder
D9: Blue; LED_0805_2012Metric_Pad1.15x1.40mm_HandSolder
D10: Green; LED_0805_2012Metric_Pad1.15x1.40mm_HandSolder
F1: 5A; CamdenBoss CFH02_W Fuse Holder
F2: 315mA; CamdenBoss CFH02_W Fuse Holder
F3: 630mA; CamdenBoss CFH02_W Fuse Holder
H1, H2, H3, H4: MountingHole; MountingHole_3.2mm_M3
J1: Batt; Molex_KK-254_AE-6410-04A_1x04_P2.54mm_Vertical
J2: PWR OUT; PinHeader_1x08_P2.54mm_Vertical
J3: TS Switch; Molex_KK-254_AE-6410-03A_1x03_P2.54mm_Vertical
J4: LV Switch A; Molex_KK-254_AE-6410-03A_1x03_P2.54mm_Vertical
J5: LV Switch B; Molex_KK-254_AE-6410-03A_1x03_P2.54mm_Vertical
J6: Batt_Lvl; PinHeader_1x02_P2.54mm_Vertical
L1, L2: 33u; L_12x12mm_H6mm
R1, R4: 1k; R_0805_2012Metric_Pad1.20x1.40mm_HandSolder
R2: 68; R_0805_2012Metric_Pad1.20x1.40mm_HandSolder
R3: 3k; R_0805_2012Metric_Pad1.20x1.40mm_HandSolder
R5: 82; R_0805_2012Metric_Pad1.20x1.40mm_HandSolder
R6: 1k6; R_0805_2012Metric_Pad1.20x1.40mm_HandSolder
R7, R8: 680; R_0805_2012Metric_Pad1.20x1.40mm_HandSolder
R9: 160; R_0805_2012Metric_Pad1.20x1.40mm_HandSolder
R10: 75; R_0805_2012Metric_Pad1.20x1.40mm_HandSolder
R11: 390k; R_0805_2012Metric_Pad1.20x1.40mm_HandSolder
R12: 110k; R_0805_2012Metric_Pad1.20x1.40mm_HandSolder
R13, R14, R15: 10k; R_0805_2012Metric_Pad1.20x1.40mm_HandSolder
U1, U2: LM2596S-ADJ; TO-263-5_TabPin3
U3: TL071; DIP-8_W7.62mm_LongPads

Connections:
+3V3: J2.2, J2.7, J5.2, R10.1, U3.7 (V+)
+3V3_Reg: D6.1 (K), F3.1, J5.3, R6.2
+5V: J2.3, J2.6, J4.2, R9.1
+5V_Reg: D4.1 (K), F2.1, J4.3, R3.2
+12V: J2.4, J2.5, J3.2, R8.1, R11.1
+BATT: C1.1, C3.1, D1.1 (K), D2.1 (K), J3.3, R7.1, U1.1 (VIN), U2.1 (VIN)
+Vin: F1.1, J1.1, J1.4
Batt_Lvl: J6.1, J6.2, U3.2 (-), U3.6
GND: C1.2, C2.2, C3.2, C4.2, D2.2 (A), D3.2 (A), D4.2 (A), D5.2 (A), D6.2 (A), D7.1 (K), D8.1 (K), D9.1 (K), D10.1 (K), J1.2, J1.3, J2.1, J2.8, R1.2, R4.2, R12.2, R13.2, R14.2, R15.2, U1.3 (GND), U1.5 (~ON/OFF), U2.3 (GND), U2.5 (~ON/OFF), U3.4 (V-)
unnamed: C2.1, F2.2, L1.2
unnamed: C4.1, F3.2, L2.2
unnamed: D1.2 (A), F1.2
unnamed: D3.1 (K), L1.1, U1.2 (OUT)
unnamed: D5.1 (K), L2.1, U2.2 (OUT)
unnamed: D7.2 (A), R7.2
unnamed: D8.2 (A), R8.2
unnamed: D9.2 (A), R9.2
unnamed: D10.2 (A), R10.2
unnamed: J3.1, R13.1
unnamed: J4.1, R14.1
unnamed: J5.1, R15.1
unnamed: R2.2, R3.1
unnamed: R5.2, R6.1
unnamed: R1.1, R2.1, U1.4 (FB)
unnamed: R4.1, R5.1, U2.4 (FB)
unnamed: R11.2, R12.1, U3.3 (+)

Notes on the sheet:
Mounting Holes
Power Input
Indicator LEDs
Power Output
Signal Output
Switch Connectors
Batt Level Gen
Protection & Regulation

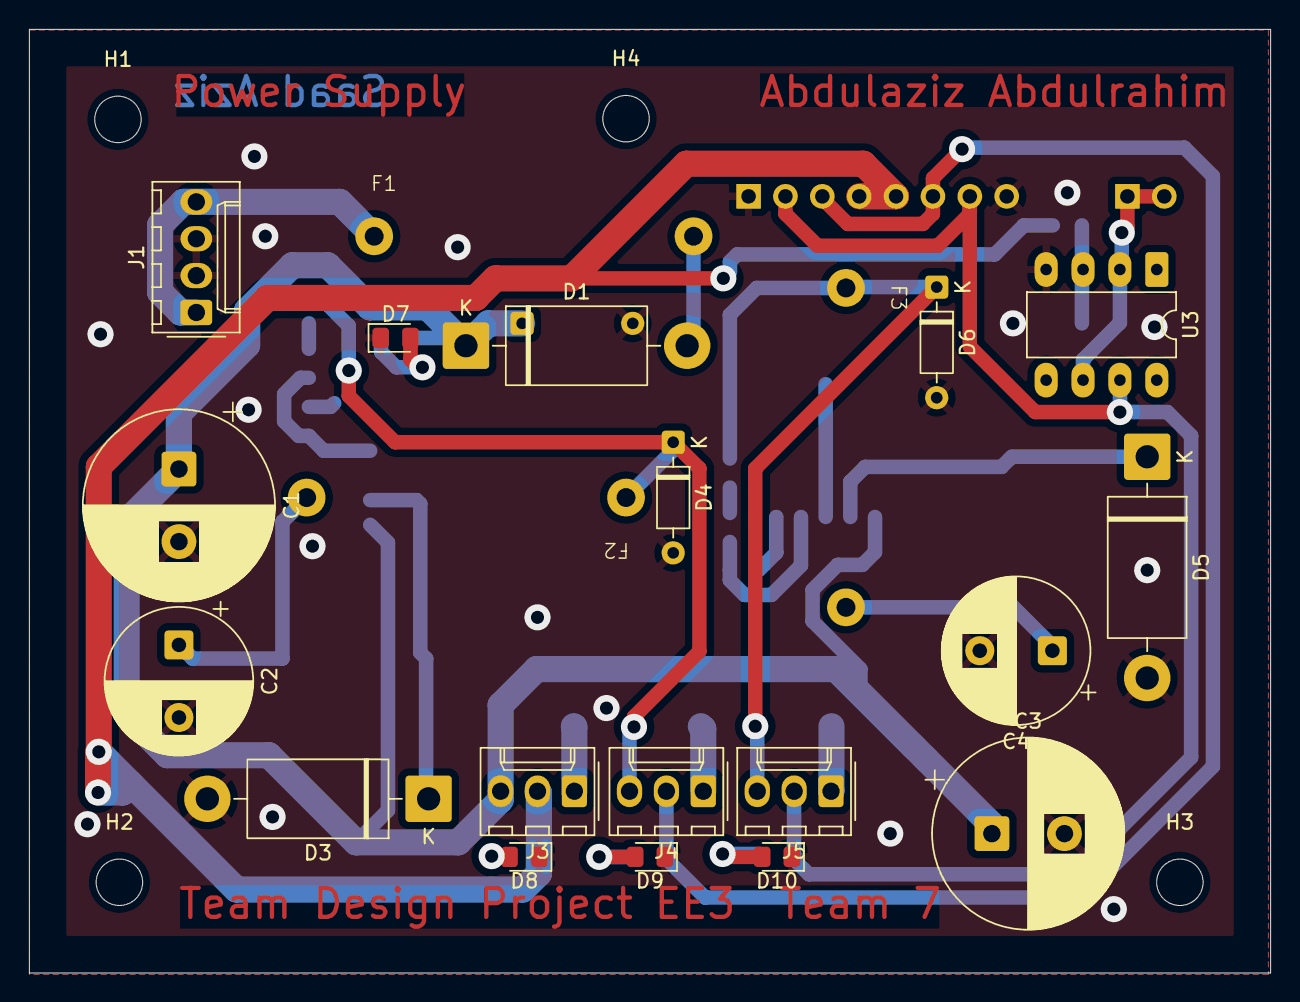
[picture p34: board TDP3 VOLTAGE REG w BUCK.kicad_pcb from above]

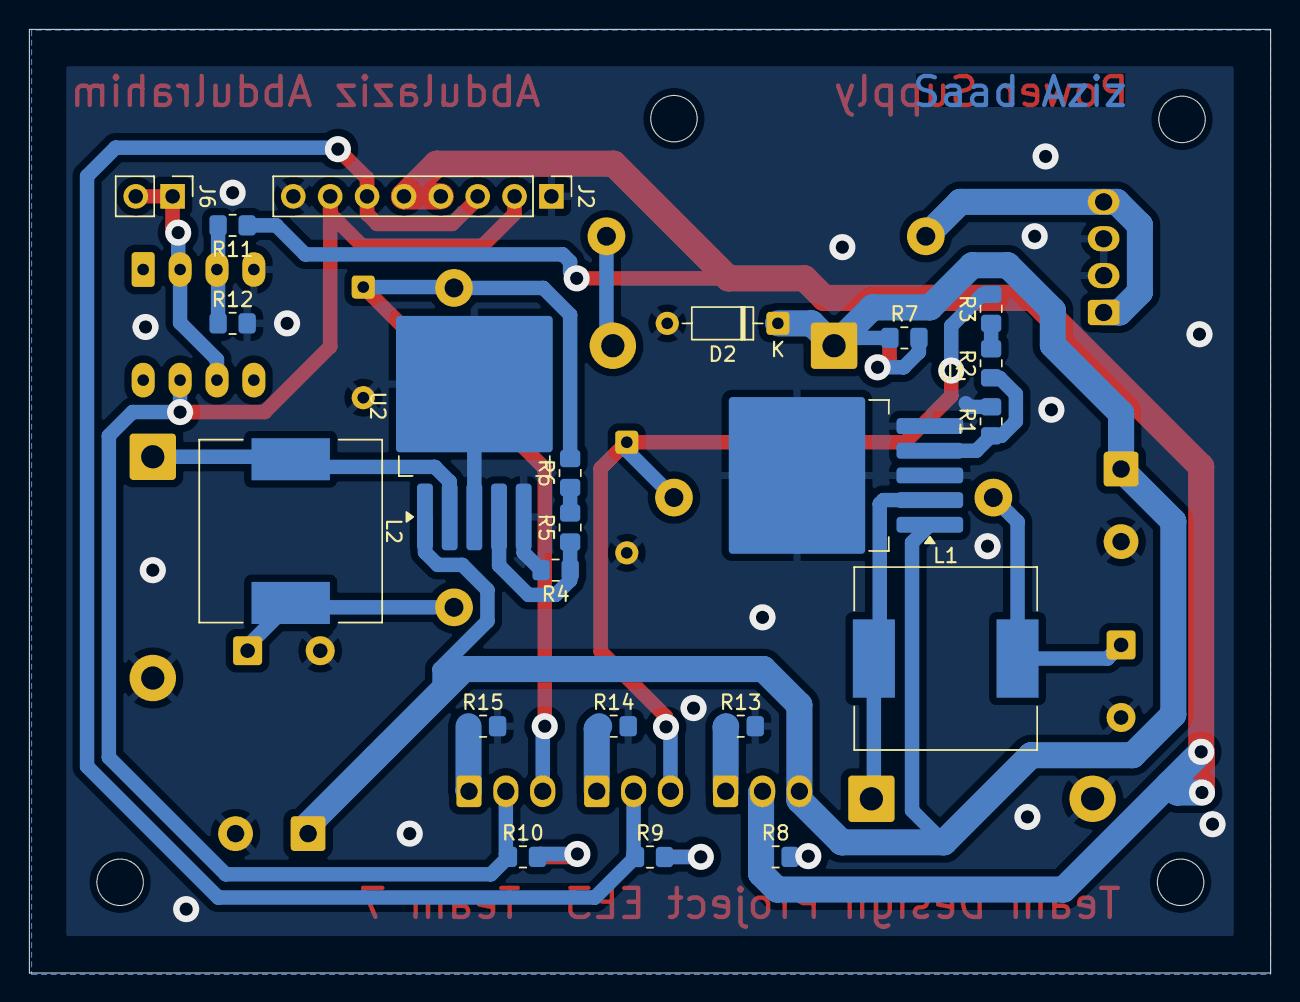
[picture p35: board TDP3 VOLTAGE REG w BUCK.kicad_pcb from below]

Board: 2 copper layers, 85.5 x 65.0 mm, 47 parts (22 on the bottom side), 26 nets.

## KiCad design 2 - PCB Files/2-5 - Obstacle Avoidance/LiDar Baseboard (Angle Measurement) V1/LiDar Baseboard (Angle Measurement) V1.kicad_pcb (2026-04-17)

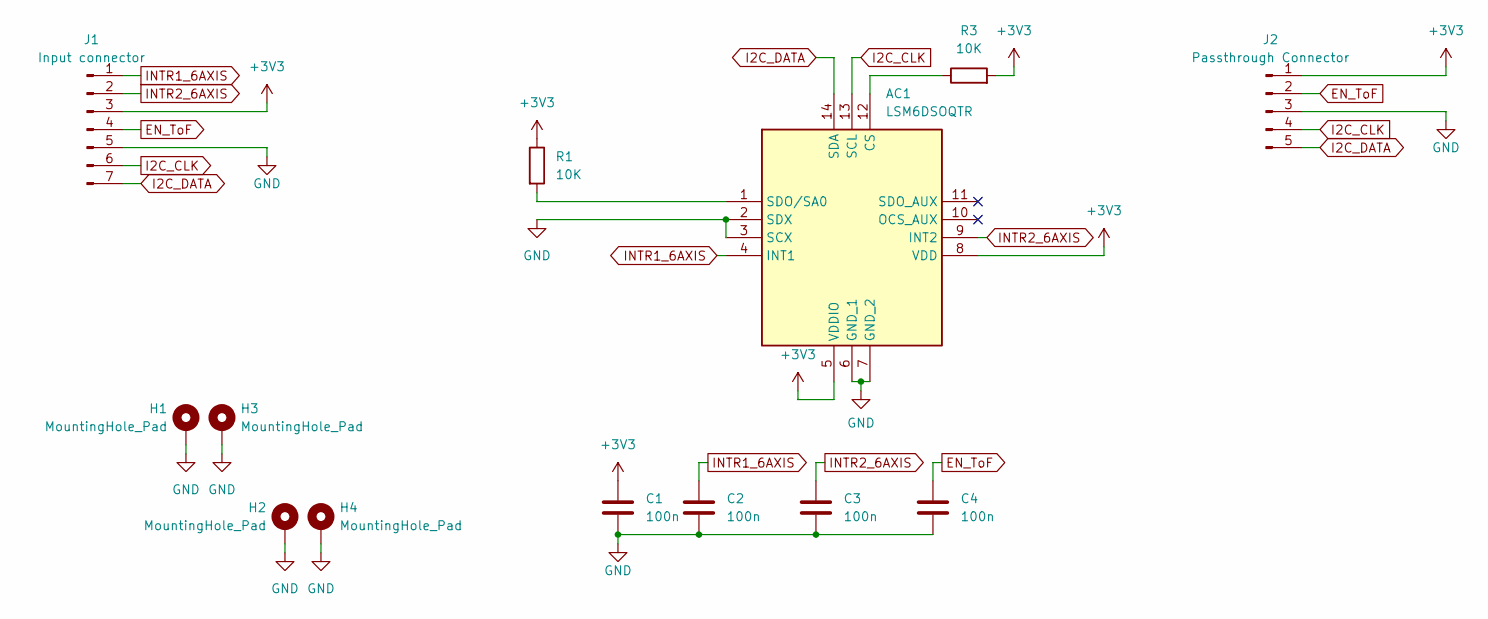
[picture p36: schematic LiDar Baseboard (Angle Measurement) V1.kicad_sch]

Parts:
AC1: LSM6DSOQTR; LSM6DSO_Breakout; Manufacturer_Part_Number LSM6DSOTR; Mouser Part Number 511-LSM6DSOTR
C1, C2, C3, C4: 100n; C_0805_2012Metric_Pad1.18x1.45mm_HandSolder
H1, H2, H3, H4: MountingHole_Pad; MountingHole_3.2mm_M3_DIN965_Pad_TopBottom
J1: Input connector; PinHeader_1x07_P2.54mm_Vertical
J2: Passthrough Connector; PinHeader_1x05_P2.54mm_Vertical
R1, R3: 10K; R_0805_2012Metric_Pad1.20x1.40mm_HandSolder

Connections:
+3V3: AC1.5 (VDDIO), AC1.8 (VDD), C1.1, J1.3, J2.1, R1.1, R3.2
EN_ToF: C4.1, J1.4, J2.2
GND: AC1.2 (SDX), AC1.3 (SCX), AC1.6 (GND_1), AC1.7 (GND_2), C1.2, C2.2, C3.2, C4.2, H1.1, H2.1, H3.1, H4.1, J1.5, J2.3; also elsewhere on the board
I2C_CLK: AC1.13 (SCL), J1.6, J2.4
I2C_DATA: AC1.14 (SDA), J1.7, J2.5
INTR1_6AXIS: AC1.4 (INT1), C2.1, J1.1
INTR2_6AXIS: AC1.9 (INT2), C3.1, J1.2
unnamed: AC1.12 (CS), R3.1
unnamed 8: AC1.1 (SDO/SA0), R1.2; also elsewhere on the board

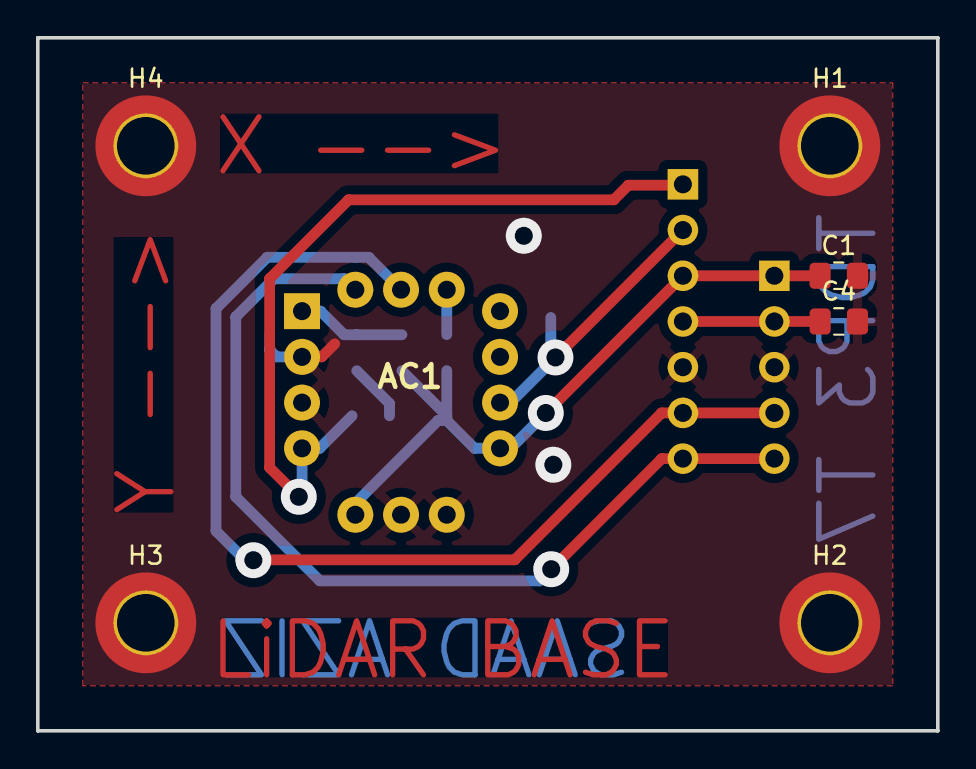
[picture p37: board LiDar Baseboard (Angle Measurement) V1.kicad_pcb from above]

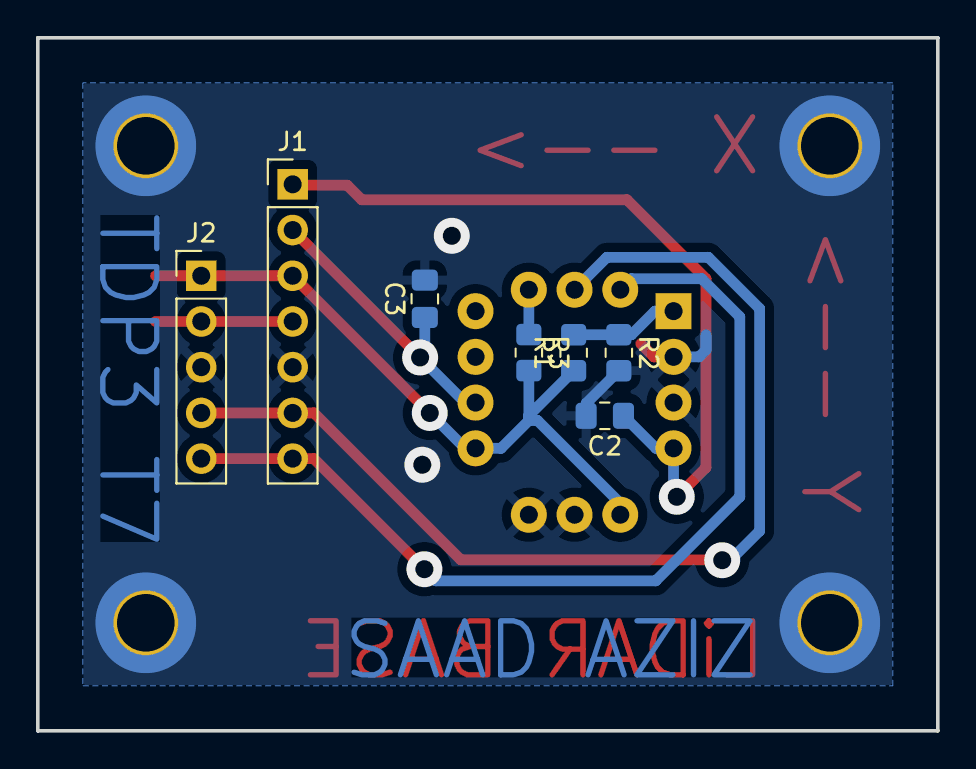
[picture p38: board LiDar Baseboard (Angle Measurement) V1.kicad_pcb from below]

Board: 2 copper layers, 50.0 x 38.5 mm, 14 parts (7 on the bottom side), 9 nets.

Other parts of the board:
R2: 10K; R_0805_2012Metric_Pad1.20x1.40mm_HandSolder

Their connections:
GND: R2.2; also elsewhere on the board
unnamed 8: R2.1; also elsewhere on the board

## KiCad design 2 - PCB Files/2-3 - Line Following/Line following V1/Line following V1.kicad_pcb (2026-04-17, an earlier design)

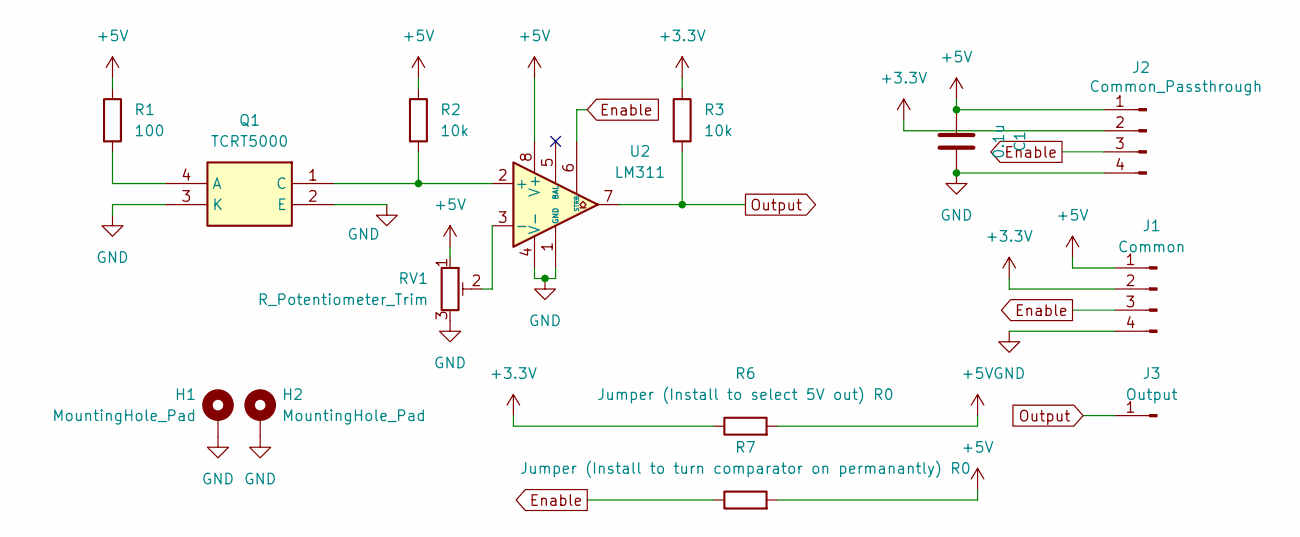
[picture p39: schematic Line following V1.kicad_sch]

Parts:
C1: 0.1u; C_0805_2012Metric_Pad1.18x1.45mm_HandSolder
H1, H2: MountingHole_Pad; MountingHole_5.3mm_M5_DIN965_Pad_TopBottom
J1: Common; PinHeader_1x04_P2.54mm_Vertical
J2: Common_Passthrough; PinHeader_1x04_P2.54mm_Vertical
J3: Output; PinHeader_1x01_P2.54mm_Vertical
Q1: TCRT5000; Manufacturer_Part_Number TCRT5000
R1: 100; R_0805_2012Metric_Pad1.20x1.40mm_HandSolder
R2, R3: 10k; R_0805_2012Metric_Pad1.20x1.40mm_HandSolder
R6: Jumper (Install to select 5V out) R0; R_0805_2012Metric_Pad1.20x1.40mm_HandSolder
R7: Jumper (Install to turn comparator on permanantly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; R_0805_2012Metric_Pad1.20x1.40mm_HandSolder
RV1: R_Potentiometer_Trim; Potentiometer_Bourns_3266W_Vertical
U2: LM311; DIP-8_W7.62mm_LongPads

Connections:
+3.3V: J1.2, J2.2, R3.1, R6.1
+5V: C1.2, J1.1, J2.1, R1.1, R2.1, R6.2, R7.2, RV1.1, U2.8 (V+)
Enable: J1.3, J2.3, R7.1, U2.6 (STRB)
GND: C1.1, H1.1, H2.1, J1.4, J2.4, Q1.2 (E), Q1.3 (K), RV1.3, U2.1 (GND), U2.4 (V-)
unnamed: Q1.4 (A), R1.2
unnamed: Q1.1 (C), R2.2, U2.2 (+)
unnamed: RV1.2, U2.3 (-)
Output: J3.1, R3.2, U2.7

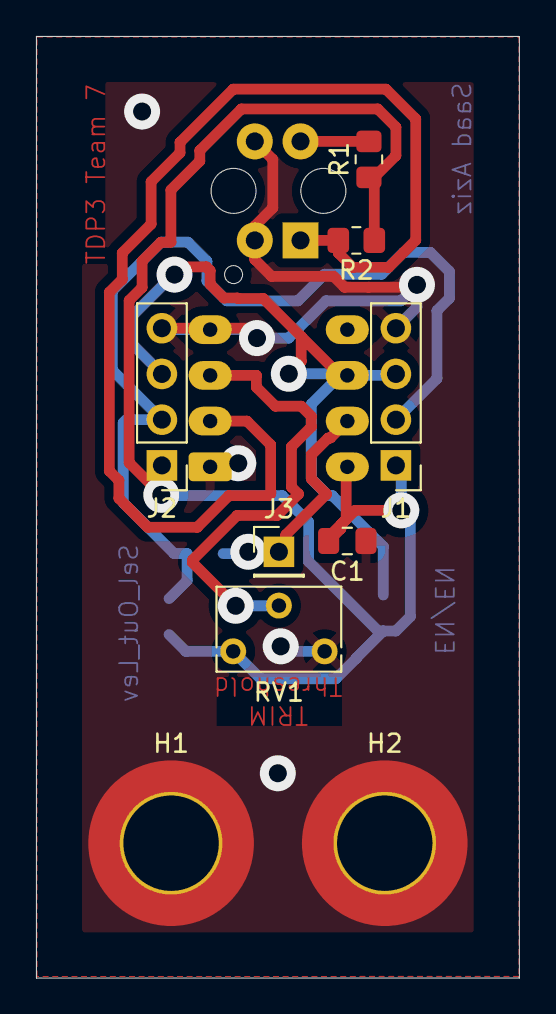
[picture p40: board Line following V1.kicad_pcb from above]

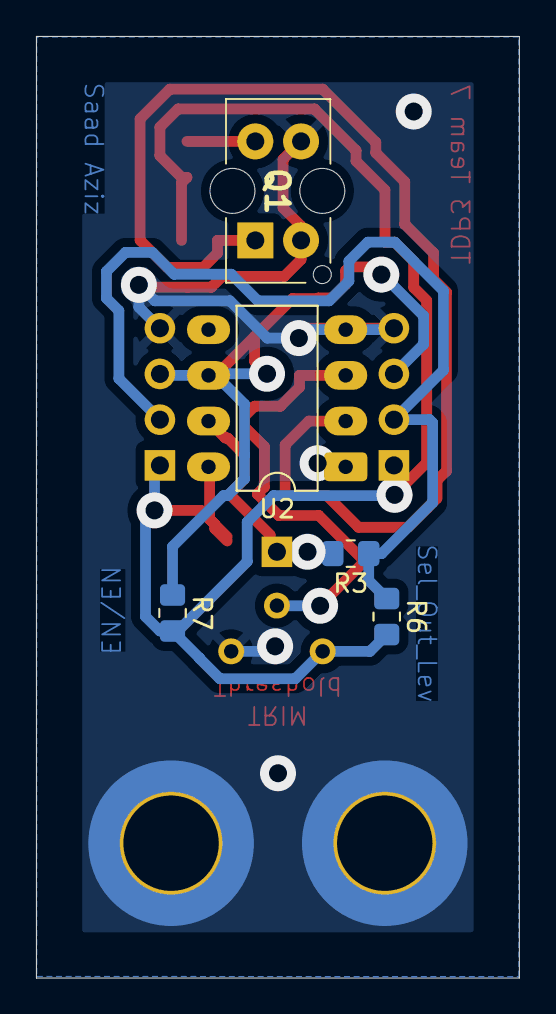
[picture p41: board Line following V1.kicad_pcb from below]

Board: 2 copper layers, 26.8 x 52.3 mm, 14 parts (5 on the bottom side), 8 nets.

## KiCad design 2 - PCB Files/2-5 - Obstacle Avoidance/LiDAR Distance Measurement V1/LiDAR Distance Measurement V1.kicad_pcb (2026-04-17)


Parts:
C1, C2, C3: 0.1u; C_0603_1608Metric
H1, H2: MountingHole_Pad; MountingHole_3.2mm_M3_DIN965_Pad_TopBottom
J1: Conn_01x05_Pin; PinHeader_1x05_P2.54mm_Vertical
R1: 10k; R_0805_2012Metric_Pad1.20x1.40mm_HandSolder; not fitted
R2, R3: 4k7; R_0805_2012Metric_Pad1.20x1.40mm_HandSolder; not fitted
U1: TMF8806-1AM_OLGA12_LF_T&RDP; TMF88061AMOLGA12LFTRDP; Manufacturer_Part_Number TMF8806-1AM OLGA12 LF T&RDP

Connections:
+3V3: C1.1, C2.2, C3.1, J1.1, R1.1, R2.1, R3.1, U1.1 (VDDC), U1.3 (GPIO0), U1.7 (VDD), U1.12 (VDDV)
EN_ToF: J1.2, R1.2, U1.9 (EN)
GND: C1.2, C2.1, C3.2, H1.1, H2.1, J1.3, U1.2 (GNDC), U1.4 (INT), U1.8 (GND), U1.10 (GPIO1), U1.11 (GNDV)
I2C_CLK: J1.4, R2.2, U1.5 (SCL)
I2C_DATA: J1.5, R3.2, U1.6 (SDA)

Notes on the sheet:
Test Pull-Up, Remove for normal operation


Board: 2 copper layers, 29.5 x 25.8 mm, 10 parts (1 on the bottom side), 5 nets.

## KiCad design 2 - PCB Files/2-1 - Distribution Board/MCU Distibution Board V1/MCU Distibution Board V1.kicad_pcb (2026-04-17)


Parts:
H1, H2, H3, H4: MountingHole; MountingHole_3.2mm_M3
J1, J9: Conn_02x08_Odd_Even; PinSocket_2x08_P2.54mm_Vertical
J2: Conn_02x10_Odd_Even; PinSocket_2x10_P2.54mm_Vertical
J4: PWR; Molex_KK-254_AE-6410-04A_1x04_P2.54mm_Vertical
J10: Conn_02x06_Odd_Even; PinSocket_2x06_P2.54mm_Vertical
J100: FRDM-KL25Z
R1: 10k; R_0805_2012Metric_Pad1.20x1.40mm_HandSolder
SW1: SW_DPST; SW_Push_2P1T_Toggle_CK_PVA1xxH1xxxxxxV2

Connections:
+3V3: J9.4, J9.8, J100.J9-4 (P3V3), J100.J9-8 (P3V3), R1.1
+5V: J4.2, J4.3, J9.10, J9.16, J100.J9-10 (P5V_USB), J100.J9-16 (P5-9V_VIN)
GND: J2.14, J4.1, J4.4, J9.12, J9.14, J100.J2-14 (GND), J100.J9-12 (GND), J100.J9-14 (GND), SW1.1, SW1.3
NRST: J9.6, J100.J9-6 (RESET/PTA20), R1.2, SW1.2, SW1.4
PTA1: J1.2, J100.J1-2 (PTA1)
PTA2: J1.4, J100.J1-4 (PTA2)
PTA4: J1.10, J100.J1-10 (PTA4)
PTA5: J1.12, J100.J1-12 (PTA5)
PTA12: J1.8, J100.J1-8 (PTA12)
PTA13: J2.2, J100.J2-2 (PTA13)
PTA16: J2.9, J100.J2-9 (PTA16)
PTA17: J2.11, J100.J2-11 (PTA17)
PTB0: J10.2, J100.J10-2 (PTB0)
PTB1: J10.4, J100.J10-4 (PTB1)
PTB2: J10.6, J100.J10-6 (PTB2)
PTB3: J10.8, J100.J10-8 (PTB3)
PTB8: J9.1, J100.J9-1 (PTB8)
PTB9: J9.3, J100.J9-3 (PTB9)
PTB10: J9.5, J100.J9-5 (PTB10)
PTB11: J9.7, J100.J9-7 (PTB11)
PTC0: J1.3, J100.J1-3 (PTC0)
PTC1: J10.12, J100.J10-12 (PTC1)
PTC2: J10.10, J100.J10-10 (PTC2)
PTC3: J1.5, J100.J1-5 (PTC3)
PTC4: J1.7, J100.J1-7 (PTC4)
PTC5: J1.9, J100.J1-9 (PTC5)
PTC6: J1.11, J100.J1-11 (PTC6)
PTC7: J1.1, J100.J1-1 (PTC7)
PTC8: J1.14, J100.J1-14 (PTC8)
PTC9: J1.16, J100.J1-16 (PTC9)
PTC10: J1.13, J100.J1-13 (PTC10)
PTC11: J1.15, J100.J1-15 (PTC11)
PTC12: J2.1, J100.J2-1 (PTC12)
PTC13: J2.3, J100.J2-3 (PTC13)
PTC16: J2.5, J100.J2-5 (PTC16)
PTC17: J2.7, J100.J2-7 (PTC17)
PTD0: J2.6, J100.J2-6 (PTD0)
PTD1: J2.12, J100.J2-12 (PTD1)
PTD2: J2.8, J100.J2-8 (PTD2)
PTD3: J2.10, J100.J2-10 (PTD3)
PTD4: J1.6, J100.J1-6 (PTD4)
PTD5: J2.4, J100.J2-4 (PTD5)
PTD6: J2.17, J100.J2-17 (PTD6)
PTD7: J2.19, J100.J2-19 (PTD7)
PTE0: J2.18, J100.J2-18 (PTE1)
PTE1: J2.20, J100.J2-20 (PTE0)
PTE2: J9.9, J100.J9-9 (PTE2)
PTE3: J9.11, J100.J9-11 (PTE3)
PTE4: J9.13, J100.J9-13 (PTE4)
PTE5: J9.15, J100.J9-15 (PTE5)
PTE20: J10.1, J100.J10-1 (PTE20)
PTE21: J10.3, J100.J10-3 (PTE21)
PTE22: J10.5, J100.J10-5 (PTE22)
PTE23: J10.7, J100.J10-7 (PTE23)
PTE29: J10.9, J100.J10-9 (PTE29)
PTE30: J10.11, J100.J10-11 (PTE30)
PTE31: J2.13, J100.J2-13 (PTE31)
SDA_PTD5: J9.2, J100.J9-2 (SDA_PTD5)
VREFH: J2.16, J100.J2-16 (VREFH)

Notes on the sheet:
Mounting Holes
Power Input
Auxiliary I/O
Reset Switch
MCU Module
^ ^ (Pins here are miss labeled) PTE0 & PTE1 Swapped around



Board: 2 copper layers, 117.0 x 92.0 mm, 12 parts (5 on the bottom side), 59 nets.

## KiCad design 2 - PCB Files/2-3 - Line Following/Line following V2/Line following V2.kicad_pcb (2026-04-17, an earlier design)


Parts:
C1, C2: 0.1u; C_0805_2012Metric_Pad1.18x1.45mm_HandSolder
H1, H2: MountingHole_Pad; MountingHole_5.3mm_M5_DIN965_Pad_TopBottom
J1: I/O Molex KK; Molex_KK-254_AE-6410-08A_1x08_P2.54mm_Vertical
Q1, Q2, Q3: TCRT5000; Manufacturer_Part_Number TCRT5000
R1, R4, R7: 100; R_0805_2012Metric_Pad1.20x1.40mm_HandSolder
R2, R3, R5, R6, R8, R9, R10, R11, R12: 10k; R_0805_2012Metric_Pad1.20x1.40mm_HandSolder
U1, U2, U3: LM311; DIP-8_W7.62mm_LongPads

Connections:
+3.3V: C2.2, J1.6, R3.1, R6.1, R9.1
+5V: C1.2, J1.2, R1.1, R2.1, R4.1, R5.1, R7.1, R8.1, R10.1, R11.1, R12.1, U1.8 (V+), U2.8 (V+), U3.8 (V+)
GND: C1.1, C2.1, H1.1, H2.1, J1.1, J1.8, Q1.2 (E), Q1.3 (K), Q2.2 (E), Q2.3 (K), Q3.2 (E), Q3.3 (K), U1.1 (GND), U1.4 (V-), U2.1 (GND), U2.4 (V-), U3.1 (GND), U3.4 (V-)
unnamed: Q1.4 (A), R1.2
unnamed: Q1.1 (C), R2.2, U1.2 (+)
unnamed: Q2.4 (A), R4.2
unnamed: Q2.1 (C), R5.2, U2.2 (+)
unnamed: Q3.4 (A), R7.2
unnamed: Q3.1 (C), R8.2, U3.2 (+)
unnamed: R10.2, U1.6 (STRB)
unnamed: R11.2, U2.6 (STRB)
unnamed: R12.2, U3.6 (STRB)
Output_C: J1.4, R6.2, U2.7
Output_L: J1.3, R3.2, U1.7
Output_R: J1.5, R9.2, U3.7
Threshold: J1.7, U1.3 (-), U2.3 (-), U3.3 (-)



Board: 2 copper layers, 61.5 x 45.0 mm, 23 parts (7 on the bottom side), 16 nets.

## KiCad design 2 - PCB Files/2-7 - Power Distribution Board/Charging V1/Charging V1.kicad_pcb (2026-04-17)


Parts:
H1, H2: MountingHole; MountingHole_3.2mm_M3_DIN965
J1: Battery Input; Molex_KK-254_AE-6410-04A_1x04_P2.54mm_Vertical
J2: Charger_In; BarrelJack_GCT_DCJ200-10-A_Horizontal
J3: Output; Molex_KK-254_AE-6410-04A_1x04_P2.54mm_Vertical

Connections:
+BATT: J1.2, J1.3, J2.1, J3.2, J3.3
Batt_GND: J1.1, J1.4, J2.2
VEH_GND: J2.3, J3.1, J3.4


Board: 2 copper layers, 28.5 x 30.0 mm, 5 parts (0 on the bottom side), 3 nets.

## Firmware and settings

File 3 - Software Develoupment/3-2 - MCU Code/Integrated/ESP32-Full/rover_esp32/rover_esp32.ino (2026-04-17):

/*
 ╔═══════════════════════════════════════════════════════════════════╗
 ║        TDP EE3 Team 7  —  ESP32-WROOM-32UE Rover Controller      ║
 ║                                                                   ║
 ║  Core 0 / Task 1: HC-SR04 ranging · 74HC165 encoder · 2-D map   ║
 ║                   servo spin · obstacle-avoidance FSM            ║
 ║  Core 1 / Task 2: WiFi AP · WebSocket dashboard · UDP joystick  ║
 ║                   I²C L432KC slave RX · ADC sense/batt · UART  ║
 ╚═══════════════════════════════════════════════════════════════════╝

 Required libraries (Library Manager / PlatformIO):
   ESPAsyncWebServer  (by lacamera / me-no-dev)
   AsyncTCP           (by dvarrel  / me-no-dev)

 ─── IMPORTANT UART NOTE ────────────────────────────────────────────
 Serial (UART0, GPIO1=TX, GPIO3=RX) is the hardware connection to
 the L432KC.  USB-serial is the same UART on the ESP32, so Serial
 cannot be used for USB debug in deployment.  All diagnostic output
 is routed to the web dashboard debug panel via the WebSocket.
 ────────────────────────────────────────────────────────────────────
*/

#include <Arduino.h>
#include <WiFi.h>
#include <WiFiUDP.h>
#include <AsyncTCP.h>
#include <ESPAsyncWebServer.h>
#include <Wire.h>
#include <driver/ledc.h>
#include <stdarg.h>

// ═══════════════════════════════════════════════════════════════════
//  PIN MAP  (PCB3 schematic, page 5 of uploaded PDF)
// ═══════════════════════════════════════════════════════════════════
#define PIN_TRIG          22   // OUT  → Trig_HC04
#define PIN_ECHO          21   // IN   ← Echo_HC04
#define PIN_SERVO         19   // OUT  → Servo_Ctrl     (LEDC ch 0)
#define PIN_ENC_LATCH     12   // OUT  → Encoder_Latch  (74HC165 PL, active-LOW)
#define PIN_ENC_CLK       33   // OUT  → Encoder_Clock
#define PIN_ENC_DATA      36   // IN   ← Encoder_Data   (SENSOR_VP, input-only GPIO)
#define PIN_MEAS_INT      23   // IN   ← Dist_Meas_Intr (RISING edge from enc board)
#define PIN_OBS_ACTIVE    32   // OUT  → ObsAv_Active   (interrupt to L432KC)
#define PIN_OBS_CA1       27   // OUT  → ObsAv_CA1
#define PIN_OBS_CA2       14   // OUT  → ObsAv_CA2
#define PIN_JS_SPEED      26   // OUT  → JS_Speed       (ESP32 DAC2)
#define PIN_JS_TURN       25   // OUT  → JS_Turning     (ESP32 DAC1)
#define PIN_JS_CYCLE      18   // OUT  → JS_Cycle_Mode  (pulse per cycle)
#define PIN_FOLLOW_ME      4   // OUT  → Follow_Me_MCU  (toggle)
#define PIN_STOP           0   // OUT  → Stop_MCU       (toggle) ⚠ boot-strap pin
#define PIN_SDA           17   // I²C  → I2C_SDA
#define PIN_SCL           16   // I²C  → I2C_Clk
#define PIN_BATT          39   // IN   ← Batt_Lvl_Prot  (SENSOR_VN, input-only)
#define PIN_SENSE_L       34   // IN   ← Sense_A_Prot   (left  motor current)
#define PIN_SENSE_R       35   // IN   ← Sense_B_Prot   (right motor current)
#define PIN_BUZZER         5   // OUT  → Buzzer_MCU
// Serial (UART0): TX=GPIO1 (UART_TX_ESP), RX=GPIO3 (UART_TX_L432K from L432KC)

// ═══════════════════════════════════════════════════════════════════
//  NETWORK CONFIG
// ═══════════════════════════════════════════════════════════════════
static const char*      AP_SSID  = "TDP3 Team 7";
static const char*      AP_PASS  = "saaddideverything";
static const IPAddress  AP_IP    (192, 168, 4, 1);
static const IPAddress  AP_GW    (192, 168, 4, 1);
static const IPAddress  AP_MASK  (255, 255, 255, 0);
static const uint16_t   UDP_PORT = 4210;
static const uint8_t    KL_ADDR  = 0x50;   // ESP32 own I²C slave address (L432KC is master)

// ═══════════════════════════════════════════════════════════════════
//  HARDWARE CONSTANTS
// ═══════════════════════════════════════════════════════════════════
static const int   N_SW           = 22;
static const float DEG_PER_SW     = 360.0f / N_SW;   // ≈16.36°

// Rover sensor insets from rover body edge (mm)
static const float INSET_FRONT    =  80.0f;
static const float INSET_SIDE     = 130.0f;
static const float INSET_BACK     = 150.0f;

// Obstacle detection thresholds — raw sensor distance (mm)
static const float THR_FRONT      = 400.0f;
static const float THR_SIDE       = 300.0f;
static const float THR_BACK       = 350.0f;

// GHM-01 (12 V, 200 RPM, 620 g·cm rated)
static const float MTR_RPM_NL     = 200.0f;
static const float MTR_RPM_RT     = 177.0f;
static const float MTR_I_NL       = 0.113f;
static const float MTR_I_RT       = 0.233f;
static const float MTR_TQ_RT      = 0.06079f;  // N·m  (620 g·cm)
static const float MTR_Kt         = MTR_TQ_RT / (MTR_I_RT - MTR_I_NL);   // ≈ 0.507 N·m/A
static const float MTR_SPD_REG    = (MTR_RPM_NL - MTR_RPM_RT) / (MTR_I_RT - MTR_I_NL); // RPM/A

// Battery — 10-cell NiMH, max 14.5 V
// Voltage divider: Vin(≤15 V) → 3.3 V   ratio = 3.3/15 = 0.22
static const float VDIV           = 3.3f / 15.0f;
static const float BATT_MAX       = 14.5f;
static const float BATT_MIN       = 10.0f;   // 1.0 V/cell depleted

// Servo LEDC — 50 Hz, 16-bit, 5 % duty = 1 ms pulse = full CW spin
static const uint32_t SRV_HZ     = 50;
static const uint8_t  SRV_BITS   = 16;
static const uint32_t SRV_DUTY   = (uint32_t)(0.05f * ((1u << SRV_BITS) - 1)); // 3277

// ═══════════════════════════════════════════════════════════════════
//  DATA STRUCTURES
// ═══════════════════════════════════════════════════════════════════
enum RoverState : uint8_t {
  RS_FOLLOWING=0, RS_TURNING90, RS_SEARCHING,
  RS_TRAFFICSTOP, RS_OBSTACLEAVOID, RS_MANUAL
};

struct L432KTelem {
  uint8_t trafficLight;   // 0=unknown 1=green 2=amber 3=red
  uint8_t roverState;     // RoverState
  uint8_t errorFlags;     // bit-field
  uint8_t lineSensors;    // FL[3] LC[2] LR[1] FR[0]
};

struct MapPt { float angle; float dist; };

// ─── Single shared data block (guarded by sdMutex) ─────────────────
struct SharedData {
  MapPt      map[N_SW];
  bool       obstacleDetected;

  float      iL, iR;          // motor current  (A)
  float      tqL, tqR;        // torque         (N·m)
  float      rpmL, rpmR;      // speed          (RPM)

  float      battV;
  float      battSOC;          // %

  L432KTelem mcu;
  char       dbgBuf[1024];    // circular UART debug log

  float      pitch, roll, yaw, thr;
  uint16_t   jsBtns;
  bool       jsEnabled;
  bool       followMeOn;
  bool       stopOn;
} SD;

static SemaphoreHandle_t sdMutex;

// ─── ISR flag ────────────────────────────────────────────────────────
static volatile bool measFlag = false;
static portMUX_TYPE  muxISR   = portMUX_INITIALIZER_UNLOCKED;

void IRAM_ATTR onMeasInt() {
  portENTER_CRITICAL_ISR(&muxISR);
  measFlag = true;
  portEXIT_CRITICAL_ISR(&muxISR);
}

// ─── Task handles ────────────────────────────────────────────────────
static TaskHandle_t hTask1, hTask2;

// ─── Async server objects ─────────────────────────────────────────────
AsyncWebServer httpServer(80);
AsyncWebSocket wsServer("/ws");
WiFiUDP        udpSock;

// ═══════════════════════════════════════════════════════════════════
//  INTERNAL DEBUG LOGGER → dashboard debug panel
// ═══════════════════════════════════════════════════════════════════
static void dbg(const char* fmt, ...) {
  char line[160];
  va_list ap;
  va_start(ap, fmt);
  vsnprintf(line, sizeof(line)-2, fmt, ap);
  va_end(ap);
  strcat(line, "\n");

  if (xSemaphoreTake(sdMutex, pdMS_TO_TICKS(8)) == pdTRUE) {
    size_t cur = strlen(SD.dbgBuf), add = strlen(line);
    if (cur + add >= sizeof(SD.dbgBuf) - 1) {
      // drop oldest line
      char* nl = strchr(SD.dbgBuf, '\n');
      if (nl) memmove(SD.dbgBuf, nl+1, strlen(nl));
    }
    strncat(SD.dbgBuf, line, sizeof(SD.dbgBuf) - strlen(SD.dbgBuf) - 1);
    xSemaphoreGive(sdMutex);
  }
}

// ═══════════════════════════════════════════════════════════════════
//  SWITCH ENCODER  (3 × 74HC165 daisy-chain = 24 bits, 22 used)
//  Chain order in schematic: U3→U2→U1→DATA pin
//  First bits shifted = U3 D7..D0 (switches 17-22 + 2 unused)
//  Then U2 D7..D0 (switches 9-16), then U1 D7..D0 (switches 1-8)
// ═══════════════════════════════════════════════════════════════════
static uint32_t readEncoder() {
  uint32_t val = 0;
  // Parallel-load strobe (PL active-LOW)
  digitalWrite(PIN_ENC_LATCH, LOW);
  delayMicroseconds(5);
  digitalWrite(PIN_ENC_LATCH, HIGH);
  delayMicroseconds(5);
  // Clock out 24 bits, MSB first
  for (int i = 0; i < 24; i++) {
    val = (val << 1) | (digitalRead(PIN_ENC_DATA) ? 1u : 0u);
    digitalWrite(PIN_ENC_CLK, HIGH); delayMicroseconds(2);
    digitalWrite(PIN_ENC_CLK, LOW);  delayMicroseconds(2);
  }
  // Remap: bits arrive U3→U2→U1; re-order so bit-i = switch-(i+1)
  // After 24-clock read, lower 22 bits already map to SW1..SW22
  // (verified by calibration; reverse if sense is opposite)
  return val & 0x3FFFFFu;
}

// Returns 0-based index of first active switch, or -1
static int firstActive(uint32_t enc) {
  for (int i = 0; i < N_SW; i++) if (enc & (1u << i)) return i;
  return -1;
}

// ═══════════════════════════════════════════════════════════════════
//  HC-SR04  (blocking — lives only in Task-1)
// ═══════════════════════════════════════════════════════════════════
static float measureMM() {
  digitalWrite(PIN_TRIG, LOW);  delayMicroseconds(2);
  digitalWrite(PIN_TRIG, HIGH); delayMicroseconds(10);
  digitalWrite(PIN_TRIG, LOW);
  // 35 ms timeout ≈ 6 m
  long us = pulseIn(PIN_ECHO, HIGH, 35000);
  return (us == 0) ? -1.0f : us * 0.17150f;  // mm: (us × 343 000/2) / 1e6
}

// ═══════════════════════════════════════════════════════════════════
//  OBSTACLE GEOMETRY
// ═══════════════════════════════════════════════════════════════════
static float threshForAngle(float deg) {
  while (deg < 0)   deg += 360;
  while (deg >= 360) deg -= 360;
  if (deg <= 45 || deg >= 315) return THR_FRONT;
  if (deg >= 135 && deg <= 225) return THR_BACK;
  return THR_SIDE;
}
static bool isObstacle(int swi, float mm) {
  return (mm > 0) && (mm < threshForAngle(swi * DEG_PER_SW));
}

// ═══════════════════════════════════════════════════════════════════
//  SKID-STEER HELPER  (CA1, CA2 truth table)
// ═══════════════════════════════════════════════════════════════════
static inline void setCA(uint8_t a, uint8_t b) {
  digitalWrite(PIN_OBS_CA1, a); digitalWrite(PIN_OBS_CA2, b);
}
#define SKID_FWD()   setCA(0,0)
#define SKID_RIGHT() setCA(1,0)
#define SKID_LEFT()  setCA(0,1)
#define SKID_BACK()  setCA(1,1)

// ═══════════════════════════════════════════════════════════════════
//  TASK 1 — Obstacle Avoidance + 2-D Map  (pinned to Core 0)
// ═══════════════════════════════════════════════════════════════════
static void task1(void*) {
  dbg("[T1] Core %d: obstacle/map task started", xPortGetCoreID());

  // Start servo spinning continuously at 5 % duty
  ledcSetup(0, SRV_HZ, SRV_BITS);
  ledcAttachPin(PIN_SERVO, 0);
  ledcWrite(0, SRV_DUTY);
  dbg("[T1] Servo: %lu Hz, duty=%lu (5%%)", SRV_HZ, SRV_DUTY);

  // Enable measurement interrupt
  attachInterrupt(digitalPinToInterrupt(PIN_MEAS_INT), onMeasInt, RISING);
  dbg("[T1] Meas interrupt attached on GPIO%d", PIN_MEAS_INT);

  // ── Obstacle FSM state ──────────────────────────────────────────
  bool     obsActive  = false;
  int      obsStep    = 0;
  uint32_t stepStart  = 0;
  // Timings (ms) — tune to rover geometry
  const uint32_t T_BACK  =  800;
  const uint32_t T_RIGHT =  600;
  const uint32_t T_FWD   = 1200;
  const uint32_t T_LEFT  =  600;

  for (;;) {
    // ── Measurement interrupt ──────────────────────────────────────
    bool doMeas = false;
    portENTER_CRITICAL(&muxISR);
    if (measFlag) { measFlag = false; doMeas = true; }
    portEXIT_CRITICAL(&muxISR);

    if (doMeas && !obsActive) {
      uint32_t enc = readEncoder();
      int swi = firstActive(enc);
      if (swi >= 0) {
        float mm    = measureMM();
        float angle = swi * DEG_PER_SW;

        // Update 2-D map
        if (xSemaphoreTake(sdMutex, pdMS_TO_TICKS(10)) == pdTRUE) {
          SD.map[swi] = {angle, mm};
          xSemaphoreGive(sdMutex);
        }
        dbg("[T1] sw=%2d  ang=%5.1f°  dist=%6.1fmm", swi, angle, mm);

        // Front position (switch 0 = 0° = forward)
        if (swi == 0 && isObstacle(0, mm)) {
          dbg("[T1] !! OBSTACLE FRONT  dist=%.1f mm !!", mm);
          digitalWrite(PIN_OBS_ACTIVE, HIGH);   // raise interrupt to L432KC
          if (xSemaphoreTake(sdMutex, pdMS_TO_TICKS(10)) == pdTRUE) {
            SD.obstacleDetected = true;
            xSemaphoreGive(sdMutex);
          }
          obsActive = true; obsStep = 0; stepStart = millis();
        }
      }
    }

    // ── Obstacle avoidance FSM ─────────────────────────────────────
    if (obsActive) {
      uint32_t el = millis() - stepStart;
      switch (obsStep) {
        case 0: // Back up
          SKID_BACK();
          if (el > T_BACK)  { obsStep=1; stepStart=millis(); dbg("[T1] OA: back→right"); }
          break;
        case 1: // Turn right
          SKID_RIGHT();
          if (el > T_RIGHT) { obsStep=2; stepStart=millis(); dbg("[T1] OA: right→fwd");  }
          break;
        case 2: // Forward (clear the obstacle)
          SKID_FWD();
          if (el > T_FWD)   { obsStep=3; stepStart=millis(); dbg("[T1] OA: fwd→left");   }
          break;
        case 3: // Turn left to re-align
          SKID_LEFT();
          if (el > T_LEFT)  {
            obsActive = false;
            digitalWrite(PIN_OBS_ACTIVE, LOW);
            SKID_FWD();
            if (xSemaphoreTake(sdMutex, pdMS_TO_TICKS(10)) == pdTRUE) {
              SD.obstacleDetected = false;
              xSemaphoreGive(sdMutex);
            }
            dbg("[T1] OA: complete, resumed");
          }
          break;
      }
    }
    vTaskDelay(pdMS_TO_TICKS(5));
  }
}

// ═══════════════════════════════════════════════════════════════════
//  ADC TELEMETRY
// ═══════════════════════════════════════════════════════════════════
static void readTelemetry() {
  // ── Battery ───────────────────────────────────────────────────────
  float vadc = analogRead(PIN_BATT) / 4095.0f * 3.3f;
  float bV   = vadc / VDIV;
  float soc  = constrain((bV - BATT_MIN) / (BATT_MAX - BATT_MIN) * 100.0f, 0, 100);

  // ── Motor current (sense formula from spec) ────────────────────────
  // iL = SenseL.read() / (0.45 * 1.0269) / 2   (L432KC mbed normalised read 0-1)
  // ESP32 ADC gives 0-4095, convert to 0-1 first
  float sL = analogRead(PIN_SENSE_L) / 4095.0f;
  float sR = analogRead(PIN_SENSE_R) / 4095.0f;
  float iL = sL / (0.45f * 1.0269f) / 2.0f;
  float iR = sR / (0.44f * 1.0269f) / 2.0f;

  // ── Motor torque & RPM — linear model ─────────────────────────────
  auto motorCalc = [](float I, float& tq, float& rpm) {
    float Ia = max(0.0f, I - MTR_I_NL);
    tq  = MTR_Kt * Ia;
    rpm = max(0.0f, MTR_RPM_NL - MTR_SPD_REG * Ia);
  };
  float tqL,rpmL,tqR,rpmR;
  motorCalc(iL,tqL,rpmL);
  motorCalc(iR,tqR,rpmR);

  if (xSemaphoreTake(sdMutex, pdMS_TO_TICKS(10)) == pdTRUE) {
    SD.battV=bV; SD.battSOC=soc;
    SD.iL=iL; SD.iR=iR;
    SD.tqL=tqL; SD.tqR=tqR;
    SD.rpmL=rpmL; SD.rpmR=rpmR;
    xSemaphoreGive(sdMutex);
  }
}

// ═══════════════════════════════════════════════════════════════════
//  I²C SLAVE — RECEIVE FROM L432KC
//  The L432KC is the master and pushes a 4-byte telemetry packet
//  whenever any field changes.  Wire.onReceive fires in a dedicated
//  FreeRTOS task (not a true ISR), so a short-timeout mutex is safe.
// ═══════════════════════════════════════════════════════════════════
static void onReceiveFromL432K(int numBytes) {
  if (numBytes < 4) {
    // drain any partial packet
    while (Wire.available()) Wire.read();
    dbg("[I2C] Short packet from L432K: %d bytes", numBytes);
    return;
  }
  L432KTelem t;
  t.trafficLight = Wire.read();
  t.roverState   = Wire.read();
  t.errorFlags   = Wire.read();
  t.lineSensors  = Wire.read();
  // drain any extra bytes the master accidentally sent
  while (Wire.available()) Wire.read();

  if (xSemaphoreTake(sdMutex, pdMS_TO_TICKS(5)) == pdTRUE) {
    SD.mcu = t;
    xSemaphoreGive(sdMutex);
  }
  if (t.errorFlags)
    dbg("[I2C] L432K error flags: 0x%02X", t.errorFlags);
}

// ═══════════════════════════════════════════════════════════════════
//  UDP JOYSTICK PACKET (18-byte little-endian: uint16 + 4×float32)
// ═══════════════════════════════════════════════════════════════════
static bool prev7=false, prev11=false, prev12=false;

static void processJoystick(const uint8_t* buf, size_t len) {
  if (len < 18) { dbg("[UDP] Short packet: %u bytes", len); return; }

  uint16_t btns; float roll, pitch, yaw, thr;
  memcpy(&btns,  buf,      2);
  memcpy(&roll,  buf + 2,  4);
  memcpy(&pitch, buf + 6,  4);
  memcpy(&yaw,   buf + 10, 4);
  memcpy(&thr,   buf + 14, 4);

  bool b1  = (btns >>  0) & 1;   // hold to enable output
  bool b7  = (btns >>  6) & 1;   // cycle L432KC mode
  bool b11 = (btns >> 10) & 1;   // toggle follow-me
  bool b12 = (btns >> 11) & 1;   // toggle stop

  // ── DAC speed & turning ───────────────────────────────────────────
  // speed   = pitch × (−throttle)    [main × scaler]
  // turning = roll  ×  yaw           [main × scaler]
  if (b1) {
    float spd = pitch * (-thr);
    float trn = roll  *  yaw;
    dacWrite(PIN_JS_SPEED, (uint8_t)constrain((spd + 1.0f) * 127.5f, 0, 255));
    dacWrite(PIN_JS_TURN,  (uint8_t)constrain((trn + 1.0f) * 127.5f, 0, 255));
  } else {
    dacWrite(PIN_JS_SPEED, 128);   // neutral
    dacWrite(PIN_JS_TURN,  128);
  }

  // ── Button 7: cycle mode (rising edge → 50 ms pulse) ─────────────
  if (b7 && !prev7) {
    dbg("[JS] B7: cycle L432K mode");
    digitalWrite(PIN_JS_CYCLE, HIGH); vTaskDelay(pdMS_TO_TICKS(50));
    digitalWrite(PIN_JS_CYCLE, LOW);
  }
  prev7 = b7;

  // ── Button 11: toggle follow-me ───────────────────────────────────
  if (b11 && !prev11) {
    bool st;
    if (xSemaphoreTake(sdMutex, pdMS_TO_TICKS(10)) == pdTRUE) {
      SD.followMeOn = !SD.followMeOn; st=SD.followMeOn; xSemaphoreGive(sdMutex);
    }
    digitalWrite(PIN_FOLLOW_ME, st ? HIGH : LOW);
    dbg("[JS] B11: Follow-Me %s", st?"ON":"OFF");
  }
  prev11 = b11;

  // ── Button 12: toggle stop ────────────────────────────────────────
  if (b12 && !prev12) {
    bool st;
    if (xSemaphoreTake(sdMutex, pdMS_TO_TICKS(10)) == pdTRUE) {
      SD.stopOn = !SD.stopOn; st=SD.stopOn; xSemaphoreGive(sdMutex);
    }
    digitalWrite(PIN_STOP, st ? HIGH : LOW);
    dbg("[JS] B12: Stop %s", st?"ON":"OFF");
  }
  prev12 = b12;

  if (xSemaphoreTake(sdMutex, pdMS_TO_TICKS(10)) == pdTRUE) {
    SD.jsBtns=btns; SD.pitch=pitch; SD.roll=roll;
    SD.yaw=yaw; SD.thr=thr; SD.jsEnabled=b1;
    xSemaphoreGive(sdMutex);
  }
}

// ═══════════════════════════════════════════════════════════════════
//  WEBSOCKET JSON PUSH
// ═══════════════════════════════════════════════════════════════════
static void pushWS() {
  if (wsServer.count() == 0) return;

  SharedData snap;
  if (xSemaphoreTake(sdMutex, pdMS_TO_TICKS(25)) != pdTRUE) return;
  snap = SD;
  xSemaphoreGive(sdMutex);

  static const char* STATES[] = {
    "FOLLOWING","TURNING90","SEARCHING",
    "TRAFFICSTOP","OBSTACLEAVOID","MANUAL"
  };
  static const char* TLS[] = {"UNKNOWN","GREEN","AMBER","RED"};
  uint8_t rs = snap.mcu.roverState;
  uint8_t tl = snap.mcu.trafficLight;

  // Build JSON
  String j;
  j.reserve(900);
  j  = "{\"batt\":"  + String(snap.battV,2)
    + ",\"soc\":"    + String(snap.battSOC,1)
    + ",\"iL\":"     + String(snap.iL,3)
    + ",\"iR\":"     + String(snap.iR,3)
    + ",\"tqL\":"    + String(snap.tqL,4)
    + ",\"tqR\":"    + String(snap.tqR,4)
    + ",\"rpmL\":"   + String(snap.rpmL,1)
    + ",\"rpmR\":"   + String(snap.rpmR,1)
    + ",\"state\":\"" + String(rs<6?STATES[rs]:"?") + "\""
    + ",\"tl\":\""   + String(tl<4?TLS[tl]:"?") + "\""
    + ",\"err\":"    + String(snap.mcu.errorFlags)
    + ",\"line\":"   + String(snap.mcu.lineSensors)
    + ",\"obs\":"    + (snap.obstacleDetected?"true":"false")
    + ",\"jsEn\":"   + (snap.jsEnabled?"true":"false")
    + ",\"btns\":"   + String(snap.jsBtns)
    + ",\"pitch\":"  + String(snap.pitch,3)
    + ",\"roll\":"   + String(snap.roll,3)
    + ",\"yaw\":"    + String(snap.yaw,3)
    + ",\"thr\":"    + String(snap.thr,3)
    + ",\"follow\":" + (snap.followMeOn?"true":"false")
    + ",\"stop\":"   + (snap.stopOn?"true":"false")
    + ",\"map\":[";
  for (int i=0; i<N_SW; i++) {
    if (i) j += ",";
    j += "[" + String(snap.map[i].angle,1) + "," + String(snap.map[i].dist,1) + "]";
  }
  j += "],\"dbg\":\"";
  for (const char* p=snap.dbgBuf; *p; p++) {
    if      (*p=='\n') j += "\\n";
    else if (*p=='"')  j += "\\\"";
    else if (*p=='\\') j += "\\\\";
    else               j += *p;
  }
  j += "\"}";

  wsServer.textAll(j);
}

// ═══════════════════════════════════════════════════════════════════
//  DASHBOARD HTML — industrial-terminal aesthetic (stored in flash)
// ═══════════════════════════════════════════════════════════════════
static const char HTML[] PROGMEM = R"HTML(
<!DOCTYPE html><html lang="en"><head>
<meta charset="UTF-8"><meta name="viewport" content="width=device-width,initial-scale=1">
<title>TDP EE3 Team 7 — Rover</title>
<link rel="preconnect" href="https://fonts.googleapis.com">
<link href="https://fonts.googleapis.com/css2?family=Share+Tech+Mono&family=Orbitron:wght@600;900&display=swap" rel="stylesheet">
<style>
:root{
  --bg:#070d14;--panel:#0b1520;--border:#1a3a5c;--accent:#00e5ff;
  --red:#ff3a3a;--amber:#ffb300;--green:#00e676;--dim:#3a5a7a;
  --text:#b0cce0;--mono:'Share Tech Mono',monospace;--head:'Orbitron',sans-serif;
}
*{box-sizing:border-box;margin:0;padding:0}
body{background:var(--bg);color:var(--text);font-family:var(--mono);font-size:11px;height:100vh;overflow:hidden;display:flex;flex-direction:column}
/* scanline overlay */
body::after{content:'';position:fixed;inset:0;background:repeating-linear-gradient(0deg,transparent,transparent 2px,rgba(0,0,0,.15) 2px,rgba(0,0,0,.15) 4px);pointer-events:none;z-index:999}
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
void loop() { vTaskDelay(portMAX_DELAY); }   // everything runs in RTOS tasks

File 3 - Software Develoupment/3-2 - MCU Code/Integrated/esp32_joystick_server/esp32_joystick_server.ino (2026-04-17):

/*
 * ESP32 Joystick WiFi Receiver  v5  --  ACCESS POINT MODE  (3-pin output)
 * ============================================================
 * The ESP32 broadcasts its OWN WiFi network.
 * Connect your Windows laptop to that network, then run
 * joystick_client.py.  No router needed.
 *
 *   WiFi SSID     : ESP32_Joystick
 *   WiFi Password : joystick123
 *   ESP32 IP      : 192.168.4.1  (AP default, fixed)
 *   UDP port      : 4210
 *   Dashboard     : http://192.168.4.1/
 *
 * OUTPUTS:
 *   GPIO 25  -> Aout1  TURN RATE  = roll          (8-bit DAC, 0-3.3 V, centre = 1.65 V)
 *   GPIO 26  -> Aout2  SPEED      = pitch x (-throttle) (8-bit DAC, 0-3.3 V, centre = 1.65 V)
 *   GPIO 18  -> HIGH while joystick Button 1 OR Button 7 is pressed
 *
 * Board  : ESP32 Dev Module
 * Core   : ESP32 by Espressif 3.x
 * ============================================================
 */

#include <WiFi.h>
#include <WiFiUdp.h>
#include <WebServer.h>

// ---- Access Point settings --------------------------------------------------
const char*      AP_SSID     = "ESP32_Joystick";
const char*      AP_PASSWORD = "joystick123";
const IPAddress  AP_IP      (192, 168, 4, 1);
const IPAddress  AP_GATEWAY (192, 168, 4, 1);
const IPAddress  AP_SUBNET  (255, 255, 255, 0);
// -----------------------------------------------------------------------------

const uint16_t UDP_PORT    = 4210;
const uint32_t BAUD_RATE   = 115200;
const uint16_t PACKET_SIZE = 18;

// ---- Pin definitions --------------------------------------------------------
#define PIN_AOUT1   25    // DAC1 -- Turn Rate (roll)
#define PIN_AOUT2   26    // DAC2 -- Speed (pitch * -throttle)
#define PIN_BTN_OUT 18    // HIGH when Button 1 or Button 7 pressed

// Button bit positions in the 16-bit mask (0-indexed)
#define BTN1_BIT  0   // joystick button 1
#define BTN7_BIT  6   // joystick button 7

// ---- Shared state -----------------------------------------------------------
volatile float    g_roll     = 0.0f;
volatile float    g_pitch    = 0.0f;
volatile float    g_yaw      = 0.0f;
volatile float    g_throttle = 0.0f;
volatile float    g_turnRate = 0.0f;
volatile float    g_speed    = 0.0f;
volatile uint16_t g_btnMask  = 0;
volatile uint32_t g_lastPkt  = 0;

// ---- Objects ----------------------------------------------------------------
WiFiUDP   udp;
WebServer server(80);
uint8_t   packetBuf[PACKET_SIZE];

// ---- Helpers ----------------------------------------------------------------
inline uint8_t floatToDAC(float v) {
    v = constrain(v, -1.0f, 1.0f);
    return (uint8_t)((v + 1.0f) * 0.5f * 255.0f + 0.5f);
}
float readFloat(const uint8_t* b, int o) {
    float v; memcpy(&v, b + o, sizeof(float)); return v;
}
uint16_t readU16(const uint8_t* b) {
    return (uint16_t)(b[0] | (b[1] << 8));
}

// ---- Web: /data  (JSON) -----------------------------------------------------
void handleData() {
    bool live   = (millis() - g_lastPkt) < 2000;
    bool btnOut = (g_btnMask & (1 << BTN1_BIT)) || (g_btnMask & (1 << BTN7_BIT));

    String j  = "{";
    j += "\"live\":"     + String(live ? "true" : "false") + ",";
    j += "\"roll\":"     + String(g_roll,     3) + ",";
    j += "\"pitch\":"    + String(g_pitch,    3) + ",";
    j += "\"yaw\":"      + String(g_yaw,      3) + ",";
    j += "\"throttle\":" + String(g_throttle, 3) + ",";
    j += "\"turnRate\":" + String(g_turnRate, 3) + ",";
    j += "\"speed\":"    + String(g_speed,    3) + ",";
    j += "\"btnMask\":"  + String(g_btnMask)     + ",";
    j += "\"btn1\":"     + String((g_btnMask & (1 << BTN1_BIT)) ? "true" : "false") + ",";
    j += "\"btn7\":"     + String((g_btnMask & (1 << BTN7_BIT)) ? "true" : "false") + ",";
    j += "\"btnOut\":"   + String(btnOut ? "true" : "false") + ",";
    j += "\"aout1_v\":"  + String(g_turnRate * 1.65f + 1.65f, 3) + ",";
    j += "\"aout2_v\":"  + String(g_speed    * 1.65f + 1.65f, 3);
    j += "}";

    server.sendHeader("Access-Control-Allow-Origin", "*");
    server.send(200, "application/json", j);
}
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

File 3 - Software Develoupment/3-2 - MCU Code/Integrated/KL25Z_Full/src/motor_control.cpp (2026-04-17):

// motors_control.cpp
#ifndef MOTOR_CONTROL_CPP
#define MOTOR_CONTROL_CPP

#include "header.hpp"

Ticker control;

// ---- Line-following base (longitudinal) speed ---------------
// BUG FIX: baseSpeed was declared extern in the old header but never defined.
//          Defined here as a named constant; extern-declared in header.hpp.
const float BASE_SPEED = 0.40f;  // 40 % of max torque for straight-ahead travel

// ---- PI current (torque) loop parameters --------------------
float kp_torque = 2.5f;
float ki_torque = 0.1f;
float integralL = 0.0f;
float integralR = 0.0f;

// ---- Motor / L298 specifications ----------------------------
const float MAX_CURRENT_A = 1.5f;  // L298 per-channel current limit
float motorF = 0.001f;             // PWM period (1 kHz)

volatile bool updateMotors = false;

// ---- Measured quantities ------------------------------------
float measured_iL   = 0.0f;
float measured_iR   = 0.0f;
float actualTorqueL = 0.0f;
float actualTorqueR = 0.0f;

// ---- Initialisation -----------------------------------------
void initializeMotors() {
    integralL = 0.0f;
    integralR = 0.0f;
    EnL.period(motorF);
    EnR.period(motorF);
    EnL.write(0.0f);
    EnR.write(0.0f);
    control.attach(&trigControl, 20ms);  // 50 Hz motor-update loop
    dbgPrint("[MTR] Motor init complete (PWM %.0f Hz, BASE_SPEED=%.2f)\r\n",
             1.0f / motorF, BASE_SPEED);
}

void trigControl() {
    updateMotors = true;
}

// ---- Current and torque measurement -------------------------
void calcCurrentAndTorque() {
    // Two motors wired in parallel on each L298 bridge channel → divide by 2
    // Sense-resistor values: 0.45 Ω (left), 0.44 Ω (right)
    // ADC full-scale = 3.3 V; sense gain 
    measured_iL = (SenseL.read() / (0.45f * 4.909f)) / 2.0f;
    measured_iR = (SenseR.read() / (0.44f * 4.909f))/ 2.0f;

    // Torque estimate: T [g·cm] = (I − I_no_load) × Kt
    // Kt ≈ 5166 g·cm/A from datasheet stall/no-load points
    actualTorqueL = (measured_iL > 0.113f) ? (measured_iL - 0.113f) * 5166.0f : 0.0f;
    actualTorqueR = (measured_iR > 0.113f) ? (measured_iR - 0.113f) * 5166.0f : 0.0f;
}

// ---- Main motor output function -----------------------------
// lateral     : +1.0 = full right,  −1.0 = full left
// longitudinal: +1.0 = full forward, −1.0 = full reverse
void motorsOutput(float lateral, float longitudinal) {

    // 1. Skid-steer mixer
    float reqL = longitudinal + lateral;
    float reqR = longitudinal - lateral;

    // 2. Normalise to [−1, +1] while preserving the steering ratio
    float maxReq = fabs(reqL) > fabs(reqR) ? fabs(reqL) : fabs(reqR);
    if (maxReq > 1.0f) {
        reqL /= maxReq;
        reqR /= maxReq;
    }

    // 3. Set H-Bridge direction pins
    OutL1 = (reqL >= 0.0f) ? 1 : 0;
    OutL2 = (reqL >= 0.0f) ? 0 : 1;
    OutR1 = (reqR >= 0.0f) ? 1 : 0;
    OutR2 = (reqR >= 0.0f) ? 0 : 1;

    // 4. Sample current sensors
    calcCurrentAndTorque();

    // 5. Target current proportional to requested magnitude
    float target_iL = fabs(reqL) * MAX_CURRENT_A;
    float target_iR = fabs(reqR) * MAX_CURRENT_A;

    // 6. PI error terms
    float errorL = target_iL - measured_iL;
    float errorR = target_iR - measured_iR;

    // 7. Conditional integral accumulation (anti-windup before limiting)
    //    Only accumulate when not already at a PWM rail – prevents integrator
    //    charging while the output is saturated (classic back-calculation lite).
    integralL += errorL;
    integralR += errorR;

    // 8. PI output
    float pwm_L = (kp_torque * errorL) + (ki_torque * integralL);
    float pwm_R = (kp_torque * errorR) + (ki_torque * integralR);

    // 9. Clamp and symmetric anti-windup
    if (pwm_L > 0.5f) {
        pwm_L = 0.5f;
        integralL -= errorL;   // do not accumulate while at upper rail
        dbgPrint("[MTR] Left  PWM upper-rail sat (iL=%.3fA)\r\n", measured_iL);
    } else if (pwm_L < 0.0f) {
        pwm_L = 0.0f;
        integralL -= errorL;   // do not accumulate while at lower rail
    }

    if (pwm_R > 0.5f) {
        pwm_R = 0.5f;
        integralR -= errorR;
        dbgPrint("[MTR] Right PWM upper-rail sat (iR=%.3fA)\r\n", measured_iR);
    } else if (pwm_R < 0.0f) {
        pwm_R = 0.0f;
        integralR -= errorR;
    }

    // 10. Write PWM
    EnL.write(pwm_L);
    EnR.write(pwm_R);
}

// ---- Utility: reset PI integrators (call on state transitions) ----
static void resetMotorIntegrals() {
    integralL = 0.0f;
    integralR = 0.0f;
}

// ---- 90-degree pivot turn -----------------------------------
// Returns true once any forward sensor sees the line again (turn complete).
bool turn90(int direction) {
    if (direction == 1) {
        motorsOutput( 0.5f, 0.0f);   // Pivot right (L fwd, R rev)
    } else {
        motorsOutput(-0.5f, 0.0f);   // Pivot left  (L rev, R fwd)
    }
    pollLine();
    return (bool)(L1L.read() || C0L.read() || R1L.read());
}

// ---- Lost-line search manoeuvre -----------------------------
// Pivots in the direction the line was last seen; reverses if centred.
// Returns true once a forward sensor detects the line.
bool findLine() {
    const float searchTorque = 0.4f;

    if (e_prev < -0.05f) {
        motorsOutput( searchTorque, 0.0f);   // Last seen left → pivot right
    } else if (e_prev > 0.05f) {
        motorsOutput(-searchTorque, 0.0f);   // Last seen right → pivot left
    } else {
        motorsOutput( 0.0f, -searchTorque);  // Centred: reverse to find line
    }

    pollLine();
    return (bool)(L1L.read() || C0L.read() || R1L.read());
}

#endif // MOTOR_CONTROL_CPP
